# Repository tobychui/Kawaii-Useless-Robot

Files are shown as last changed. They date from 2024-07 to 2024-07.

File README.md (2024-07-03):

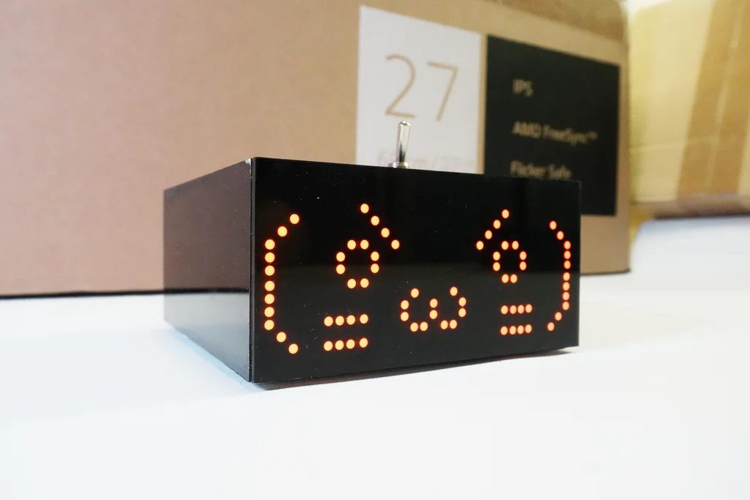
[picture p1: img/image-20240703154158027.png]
 

# Kawaii-Useless-Robot

A kawaii useless robot that runs away if you push it too hard

## Usage

There are three modes build into this robot. 

### Default Mode

Default mode is the mode where the robot interacts and response to switch pushing. To enter default mode, set the switch into the "OFF" position (lever pointing to the front-side of the robot) and power on the robot.

### AP Mode

AP mode is the mode where it will host a web server and you will be able to connect to it using mobile devices and control the robot movements and facial expression. 

For some devices like iPhone, you might need to disable mobile data and navigate to `http://192.168.4.1` with your browser to open the control panel. For most Android device, a captive portal notification should automatically pops up when you connects to it and ask you to sign in. The control UI will then be shown on the sign in captive portable browser if your network environment is valid.

### WiFi Debug Mode

You can enable WiFi (client) debug mode by setting `ENABLE_WIFI_DEBUG` to true with your home wifi crendentials.

```
#define ENABLE_WIFI_DEBUG false //Set to true to use WiFi Client mode for remote debugging
#define DEBUG_SSID "" //Debug SSID, usually your home WiFi SSID
#define DEBUG_PWD "" //Debug Password, your home WiFi Password
```

After this mode is enabled, you can connect to the web UI of the robot via your home local area network and debug any web interface issues.

## Prototype Video

IMAGE ALT TEXT HERE (https://youtu.be/l38ngzytmJw)

## Firmware Flashing

To flash firmware into this robot, open the top cover and use the type C port with a `</>` label for programming. The type C port at the back is for powering (and charging, if you builds has battery installed).

### Board Settings

ESP32 v2.014

- ESP32 Dev Module
- CPU Freq: 240Mhz
- Arduino & Events run on: Core 1
- Flash Mode: DIO

### Notes

Different version of ESP32 arduino core uses different version of RTOS. Thus, some version (specially the newer one) might have higher chances of crashing. After my testing, for the ESP32E I bought, the version v2.014 works the best. However, this might not be the same if you are getting an ESP32E with newer firmware.

## License

**Software**: MIT License

**Hardware**: CC BY-SA

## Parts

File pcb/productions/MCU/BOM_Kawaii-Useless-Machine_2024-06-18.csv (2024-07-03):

ID | Name | Designator | Footprint | Quantity | Manufacturer Part | Manufacturer | Supplier | Supplier Part | Price | link
1 | CONN-TH_2P-P2.50-XH2.54-2P | U9 | CONN-TH_2P-P2.50-XH2.54-2P | 1 | XH2.54*2P_直插 | null | LCSC | C9900008615 |  | https://lcsc.com/eda_search?q=C9900008615&%26type=1&ref=editor
2 | HDR-TH_2P-P2.54-V-M | P2 | HDR-TH_2P-P2.54-V-M | 1 | 2.54mm 1*2P | null | LCSC | C36717 | 0.006 | https://lcsc.com/eda_search?q=C36717&%26type=1&ref=editor
3 | R0805 | R34,R35,R32,R33 | R0805 | 4 | 0805W8F1002T5E | UNI-ROYAL(厚声) | LCSC | C17414 | 0.002 | https://item.szlcsc.com/142685.html
4 | C0805 | C28,C4,C7,C6,C8,C29 | C0805 | 6 | CL21A106KAYNNNE | SAMSUNG(三星) | LCSC | C15850 | 0.01 | https://item.szlcsc.com/373011.html
5 | SWITCH-SK12D07VG3 | SW1 | SWITCH-SK12D07VG3 | 1
6 | WIFI-SMD_ESP32-WROOM-32E-A | U4 | WIFI-SMD_ESP32-WROOM-32E-A | 1 | ESP32-WROOM-32E-N8R2 | ESPRESSIF(乐鑫) | LCSC | C5361945 | 3.587 | https://lcsc.com/eda_search?q=C2973652&%26type=1&ref=editor
7 | SOP-16_L10.0-W3.9-P1.27-LS6.0-BL | U7 | SOP-16_L10.0-W3.9-P1.27-LS6.0-BL | 1 |  |  | null |  |  | https://item.szlcsc.com/391677.html
8 | SOT-23-3_L2.9-W1.4-P1.90-LS2.6-BR | U11,U10 | SOT-23-3_L2.9-W1.4-P1.90-LS2.6-BR | 2 | BC817-16W | YANGJIE(扬杰) | LCSC | C968080 | 0.023 | https://atta.szlcsc.com/upload/public/pdf/source/20201201/C963380_48BF0C30091E539773A6B883B12108EF.pdf
9 | SOT-223-4_L6.5-W3.5-P2.30-LS7.0-BR | LDO1 | SOT-223-4_L6.5-W3.5-P2.30-LS7.0-BR | 1 | AMS1117-3.3 | AMS | LCSC | C6186 | 0.132 | https://item.szlcsc.com/84517.html
10 | IND-SMD_L7.3-W6.6 | L2 | IND-SMD_L7.3-W6.6 | 1 | MCS0630-1R0MPY1 | PSA(信昌电陶) | LCSC | C2937095 | 0.078 | https://lcsc.com/eda_search?q=C2937095&%26type=1&ref=editor
11 | R0805 | R5,R29 | R0805 | 2 | 0805W8F100KT5E | UNI-ROYAL(厚声) | LCSC | C25271 | 0.003 | https://lcsc.com/eda_search?q=C367831&%26type=1&ref=editor
12 | C0805 | C25,C26,C2,C23,C24 | C0805 | 5 | CC0805KRX7R9BB221 | YAGEO(国巨) | LCSC | C107145 | 0.006 | https://lcsc.com/eda_search?q=C123634&%26type=1&ref=editor
13 | C0805 | C27,C1 | C0805 | 2 | CL21A106KAYNNNE | SAMSUNG(三星) | LCSC | C15850 | 0.01 | https://lcsc.com/eda_search?q=C2835530&%26type=1&ref=editor
14 | LED0805-R-RD | LED1,LED2,LED3,LED4 | LED0805-R-RD | 4 | KT-0805W | KENTO | LCSC | C34499 | 0.016 | https://lcsc.com/eda_search?q=C84258&%26type=1&ref=editor
15 | ESOP-8_L4.9-W3.9-P1.27-LS6.0-BL-EP | U1 | ESOP-8_L4.9-W3.9-P1.27-LS6.0-BL-EP | 1 | IP5306 | INJOINIC(英集芯) | LCSC | C181692 | 0.258 | https://lcsc.com/eda_search?q=C181692&%26type=1&ref=editor
16 | R0805 | R3,R4,R1,R2 | R0805 | 4 | 0805W8F5101T5E | UNI-ROYAL(厚声) | LCSC | C27834 | 0.002 | https://lcsc.com/eda_search?q=C269736&%26type=1&ref=editor
17 | USB-C-SMD_TYPE-C-6PIN-2MD-073 | U3 | USB-C-SMD_TYPE-C-6PIN-2MD-073 | 1 | TYPE-C 16PIN 2MD(073) | SHOU HAN(首韩) | LCSC | C2765186 | 0.05 | https://lcsc.com/eda_search?q=C2765186&%26type=1&ref=editor
18 | C0805 | C3,C30 | C0805 | 2 | CC0805KRX7R9BB104 | YAGEO(国巨) | LCSC | C49678 | 0.004 | https://lcsc.com/eda_search?q=C2830721&%26type=1&ref=editor
19 | FPC-SMD_C20110 | P3,P4 | FPC-SMD_C20110 | 2 | 1.0-8P上接 | BOOMELE(博穆精密) | LCSC | C20110 | 0.09 | https://lcsc.com/eda_search?q=C20110&%26type=1&ref=editor
20 | R0805 | R6 | R0805 | 1 | RMCF0805ZT0R00 | SEI(Stackpole Electronics Inc.) | LCSC | C237773 | 0.005 | https://lcsc.com/eda_search?q=C237773&%26type=1&ref=editor
21 | TF-SMD_TF-012 | TF2 | TF-SMD_TF-012 | 1 |  |  |  |  |  | https://lcsc.com/eda_search?q=C5333937&%26type=1&ref=editor
22 | USB-C-TH_KH-TYPE-C-L6.9-6P | U6 | USB-C-TH_KH-TYPE-C-L6.9-6P | 1 | KH-TYPE-C-L6.9-6P | kinghelm(金航标) | LCSC | C2919657 | 0.137 | https://lcsc.com/eda_search?q=C2919657&%26type=1&ref=editor

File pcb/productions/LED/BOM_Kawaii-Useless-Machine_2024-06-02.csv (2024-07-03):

ID | Name | Designator | Footprint | Quantity | Manufacturer Part | Manufacturer | Supplier | Supplier Part | Price | JLCPCB Part Class | link
1 | MAX7219CWG+ | DM8,DM7,DM6,DM5,DM4,DM3,DM2,DM1 | SOIC-24_L15.4-W7.5-P1.27-LS10.3-BL | 8 | MAX7219CWG+T | ADI(亚德诺)/MAXIM(美信) | LCSC | C9964 | 2.425 | Extended Part | https://item.szlcsc.com/417060.html
2 | Header-Female-2.54_1x5 | CTRLIN | HDR-5X1/2.54 | 1 | 2.54mm 1*5p Female header | BOOMELE | LCSC | C50950 | 0.062
3 | 10uF | C1 | C0805 | 1 | CL21A106KAYNNNE | SAMSUNG(三星) | LCSC | C15850 | 0.011 | Extended Part | https://item.szlcsc.com/373011.html
4 | 100nF | C2 | C0805 | 1 | CC0805KRX7R9BB104 | YAGEO(国巨) | LCSC | C49678 | 0.004 | Extended Part | https://item.szlcsc.com/373011.html
5 | 788AS | U2,U3,U4,U5,U6,U7,U8,U1 | 788AS | 8
6 | 10kΩ | R1,R2,R3,R4,R5,R6,R7,R8 | R0805 | 8 | RMC080510K5%N | Tyohm(幸亚电阻) | LCSC | C269724 | 0.003 | Extended Part | https://lcsc.com/eda_search?q=C269724&%26type=1&ref=editor

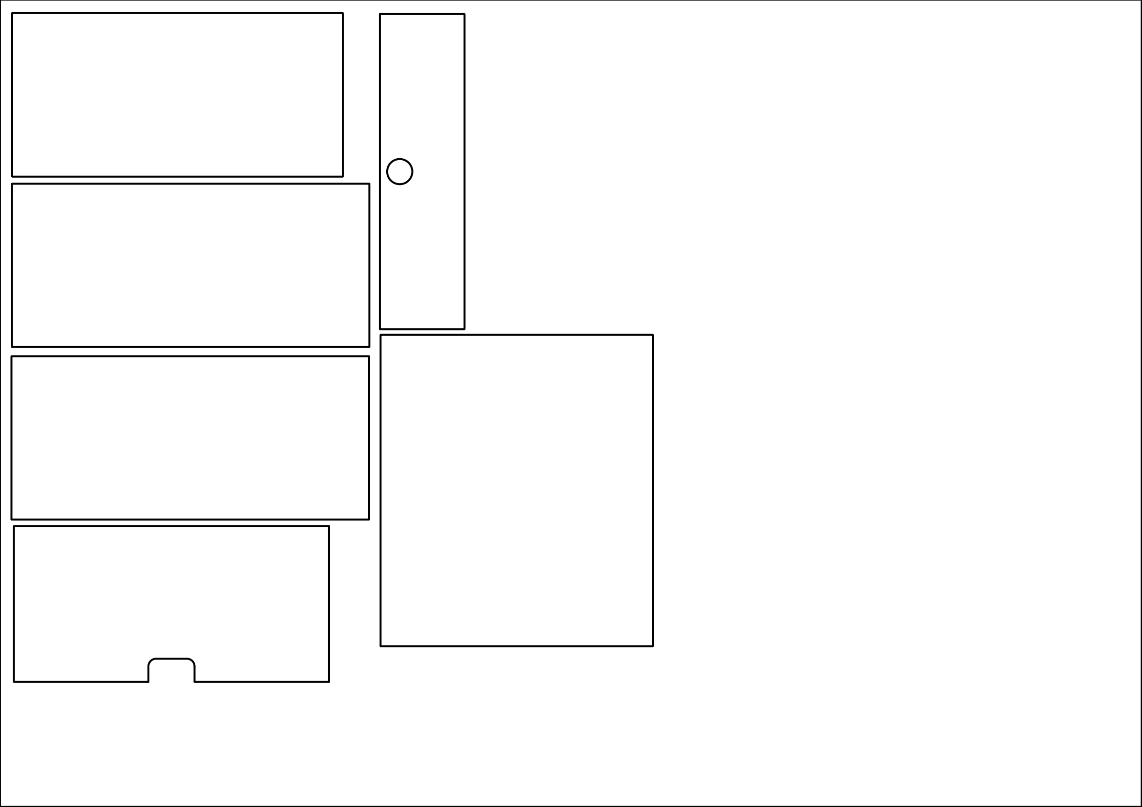
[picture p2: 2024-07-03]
lasercut/all-parts_v1-1.png

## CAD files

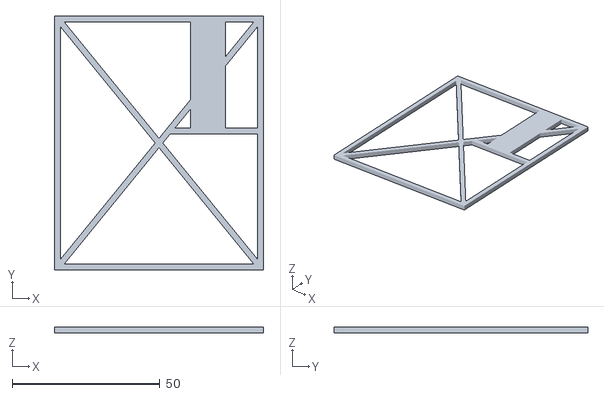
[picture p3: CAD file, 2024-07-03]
lasercut/validations/top-2.stl
70.8 x 86.0 x 2.00

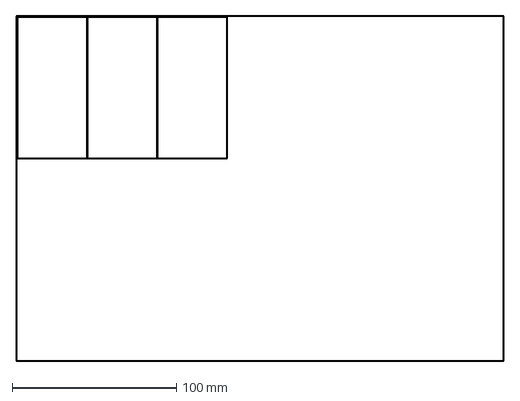
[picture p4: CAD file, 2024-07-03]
lasercut/黑透板.dxf
297.0 x 210.0 mm

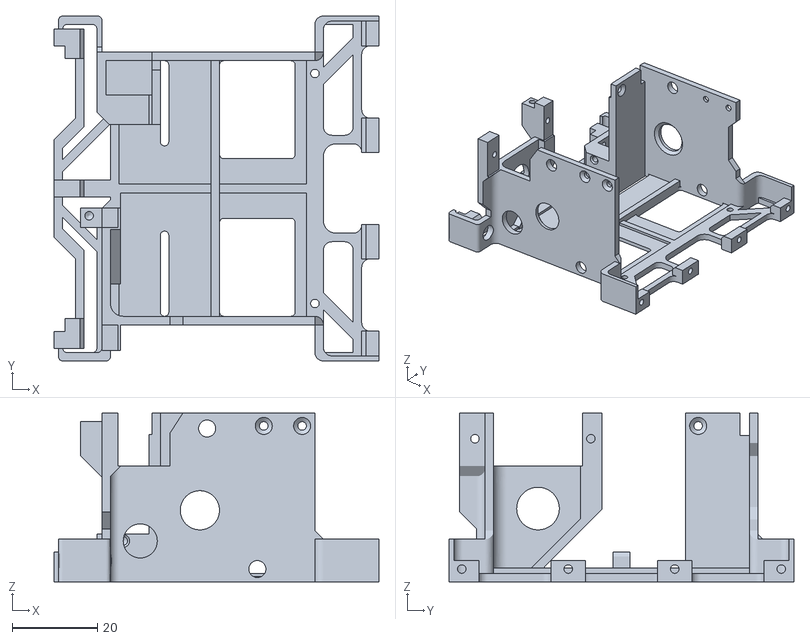
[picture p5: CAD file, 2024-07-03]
model/frame.stl
76.2 x 81.0 x 39.6

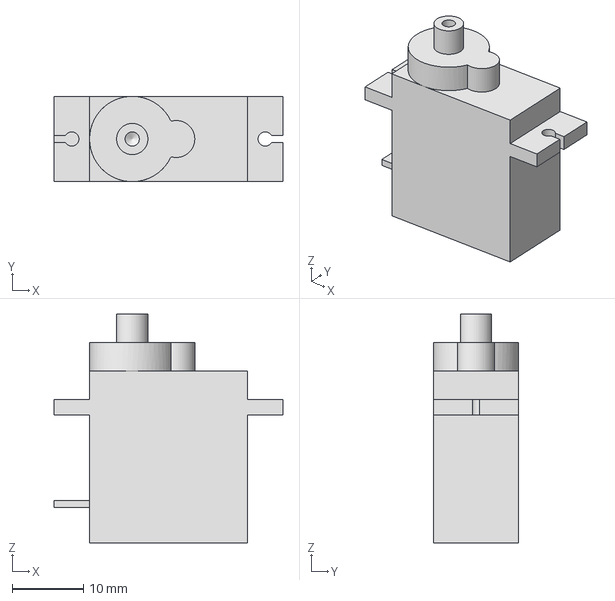
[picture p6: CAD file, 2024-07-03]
model/mockups/mg90s-servo.stp
32.2 x 12.0 x 32.2 mm

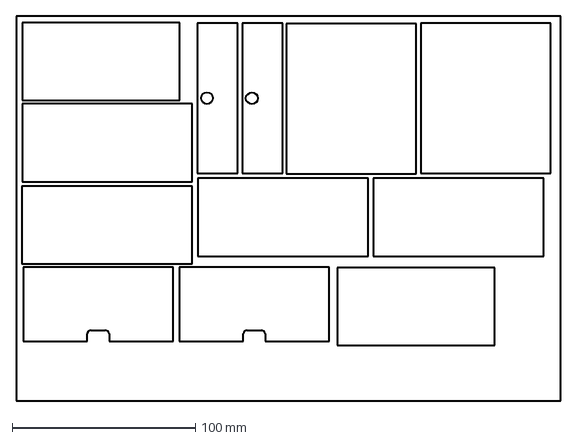
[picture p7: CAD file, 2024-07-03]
lasercut/all-parts_A4-fill.dxf
297.0 x 210.0 mm

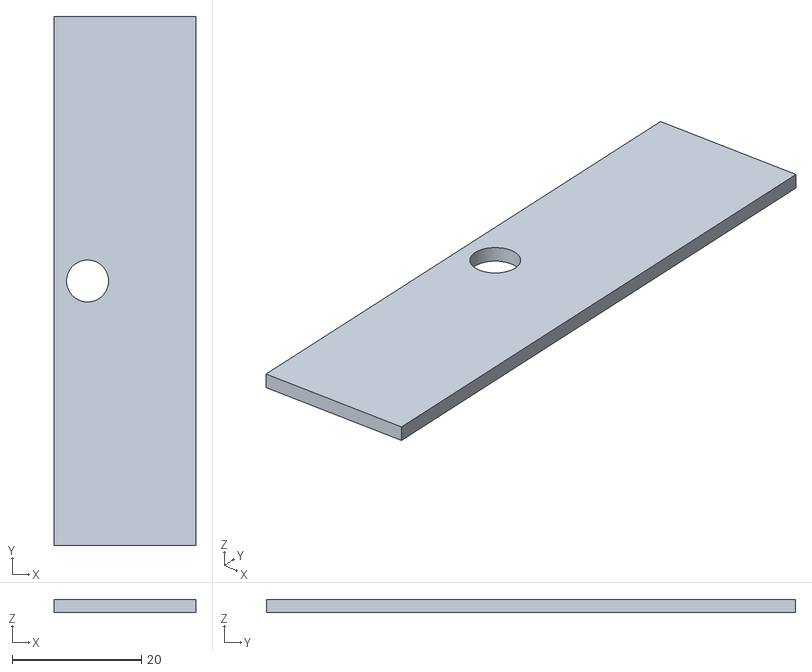
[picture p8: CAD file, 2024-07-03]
lasercut/validations/top-1.stl
22.0 x 82.0 x 2.00

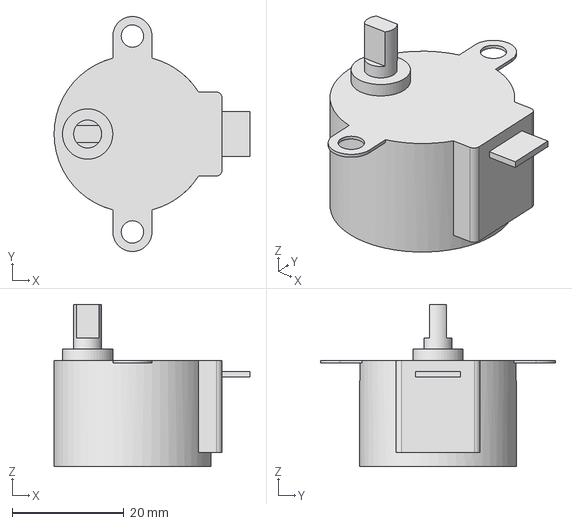
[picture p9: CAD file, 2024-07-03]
model/mockups/stepper-motor.stp
35.0 x 42.0 x 29.0 mm

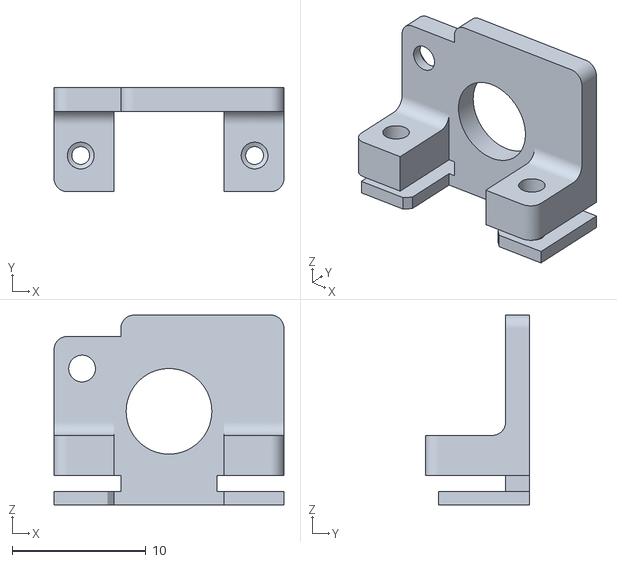
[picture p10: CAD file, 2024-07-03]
model/switch-mount.stl
17.2 x 7.80 x 14.2

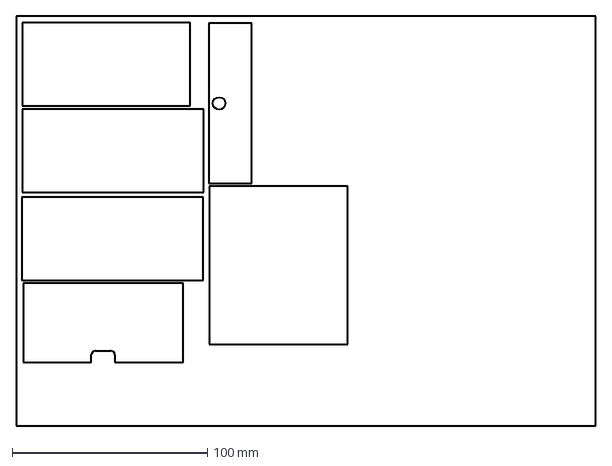
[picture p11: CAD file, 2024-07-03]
lasercut/all-parts_v1.dxf
297.0 x 210.0 mm

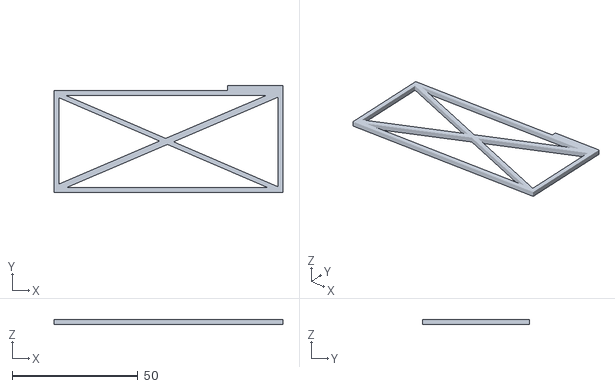
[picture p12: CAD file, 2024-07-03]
lasercut/validations/side-panels.stl
91.0 x 42.5 x 2.00

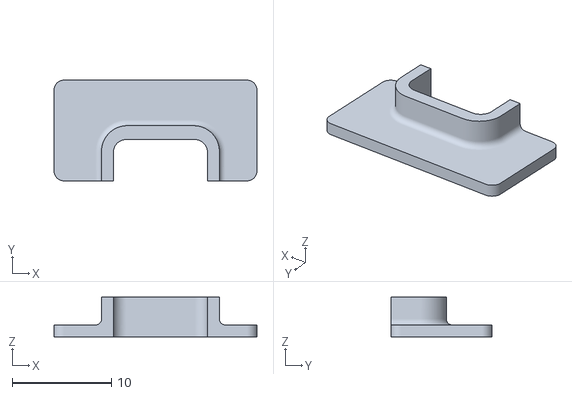
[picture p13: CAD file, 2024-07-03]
model/charge_support.stl
20.5 x 10.2 x 4.00

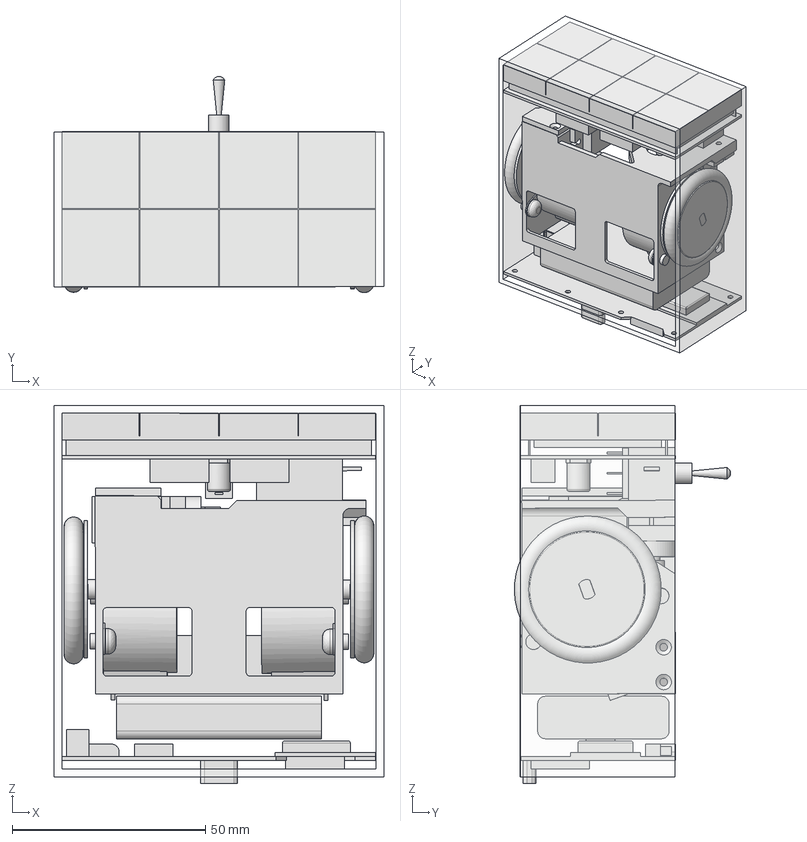
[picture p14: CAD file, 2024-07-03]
model/mockups/test-fit.stp
85.2 x 55.9 x 97.7 mm
display-unit
stepper-motor x 2
switch-mockup
mg90s-servo x 2
expected_size
battery_mockup
mcu-unit
frame v1
round m4x5 x 4
servo-mount
structural-bar
servo-swap x 2
wheel-mockup x 2
silicon-ring-mockup x 2

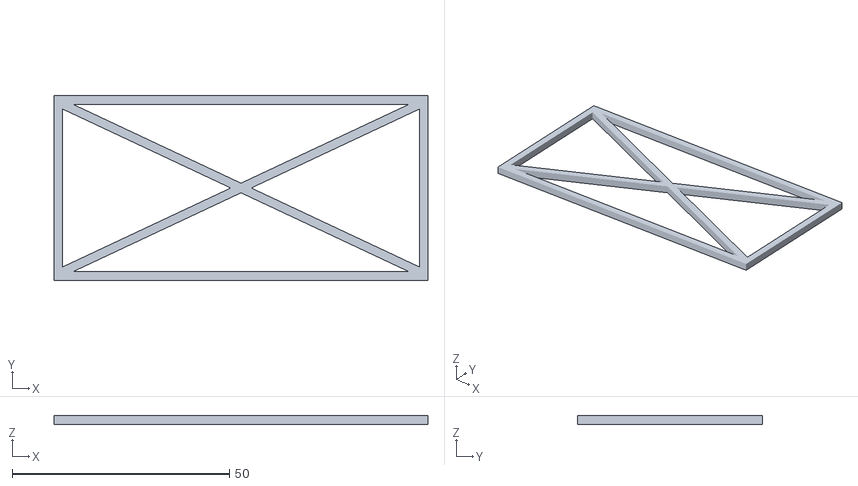
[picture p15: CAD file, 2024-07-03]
lasercut/validations/front-panel.stl
86.0 x 42.5 x 2.00

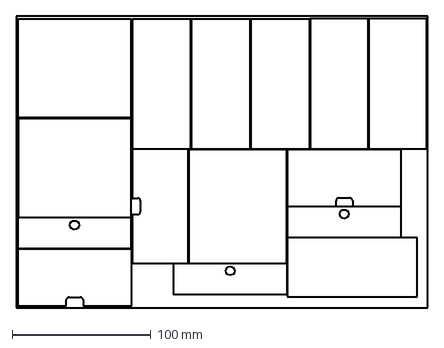
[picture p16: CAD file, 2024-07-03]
lasercut/黑板.dxf
297.0 x 210.0 mm

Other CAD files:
model/mockups/display-unit.stp
model/wheel.stl
lasercut/validations/back-panel.stl
model/mockups/switch-mockup.stp
lasercut/A4.ipt
lasercut/OldVersions/all-parts_A4-fill.0006.dwg
lasercut/OldVersions/all-parts_v1.0005.dwg
lasercut/OldVersions/all-parts_v2.0007.dwg
lasercut/OldVersions/back-panel.0008.ipt
lasercut/OldVersions/front-panel.0004.ipt
lasercut/OldVersions/side-panels.0013.ipt
lasercut/OldVersions/top-1.0008.ipt
lasercut/OldVersions/top-2.0004.ipt
lasercut/OldVersions/top-2.0006.ipt
lasercut/OldVersions/黑透板.0007.dwg
lasercut/all-parts_A4-fill.dwg
lasercut/all-parts_v1.dwg
lasercut/back-panel.ipt
lasercut/black-20x30.ipt
lasercut/front-panel.ipt
lasercut/side-panels.ipt
lasercut/top-1.ipt
lasercut/top-2.ipt
lasercut/黑板.dwg
lasercut/黑透板.dwg
model/charge_support.ipt
model/frame.ipt
model/frame_no-back-mount.ipt
model/mockups/M4x5flat.ipt
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

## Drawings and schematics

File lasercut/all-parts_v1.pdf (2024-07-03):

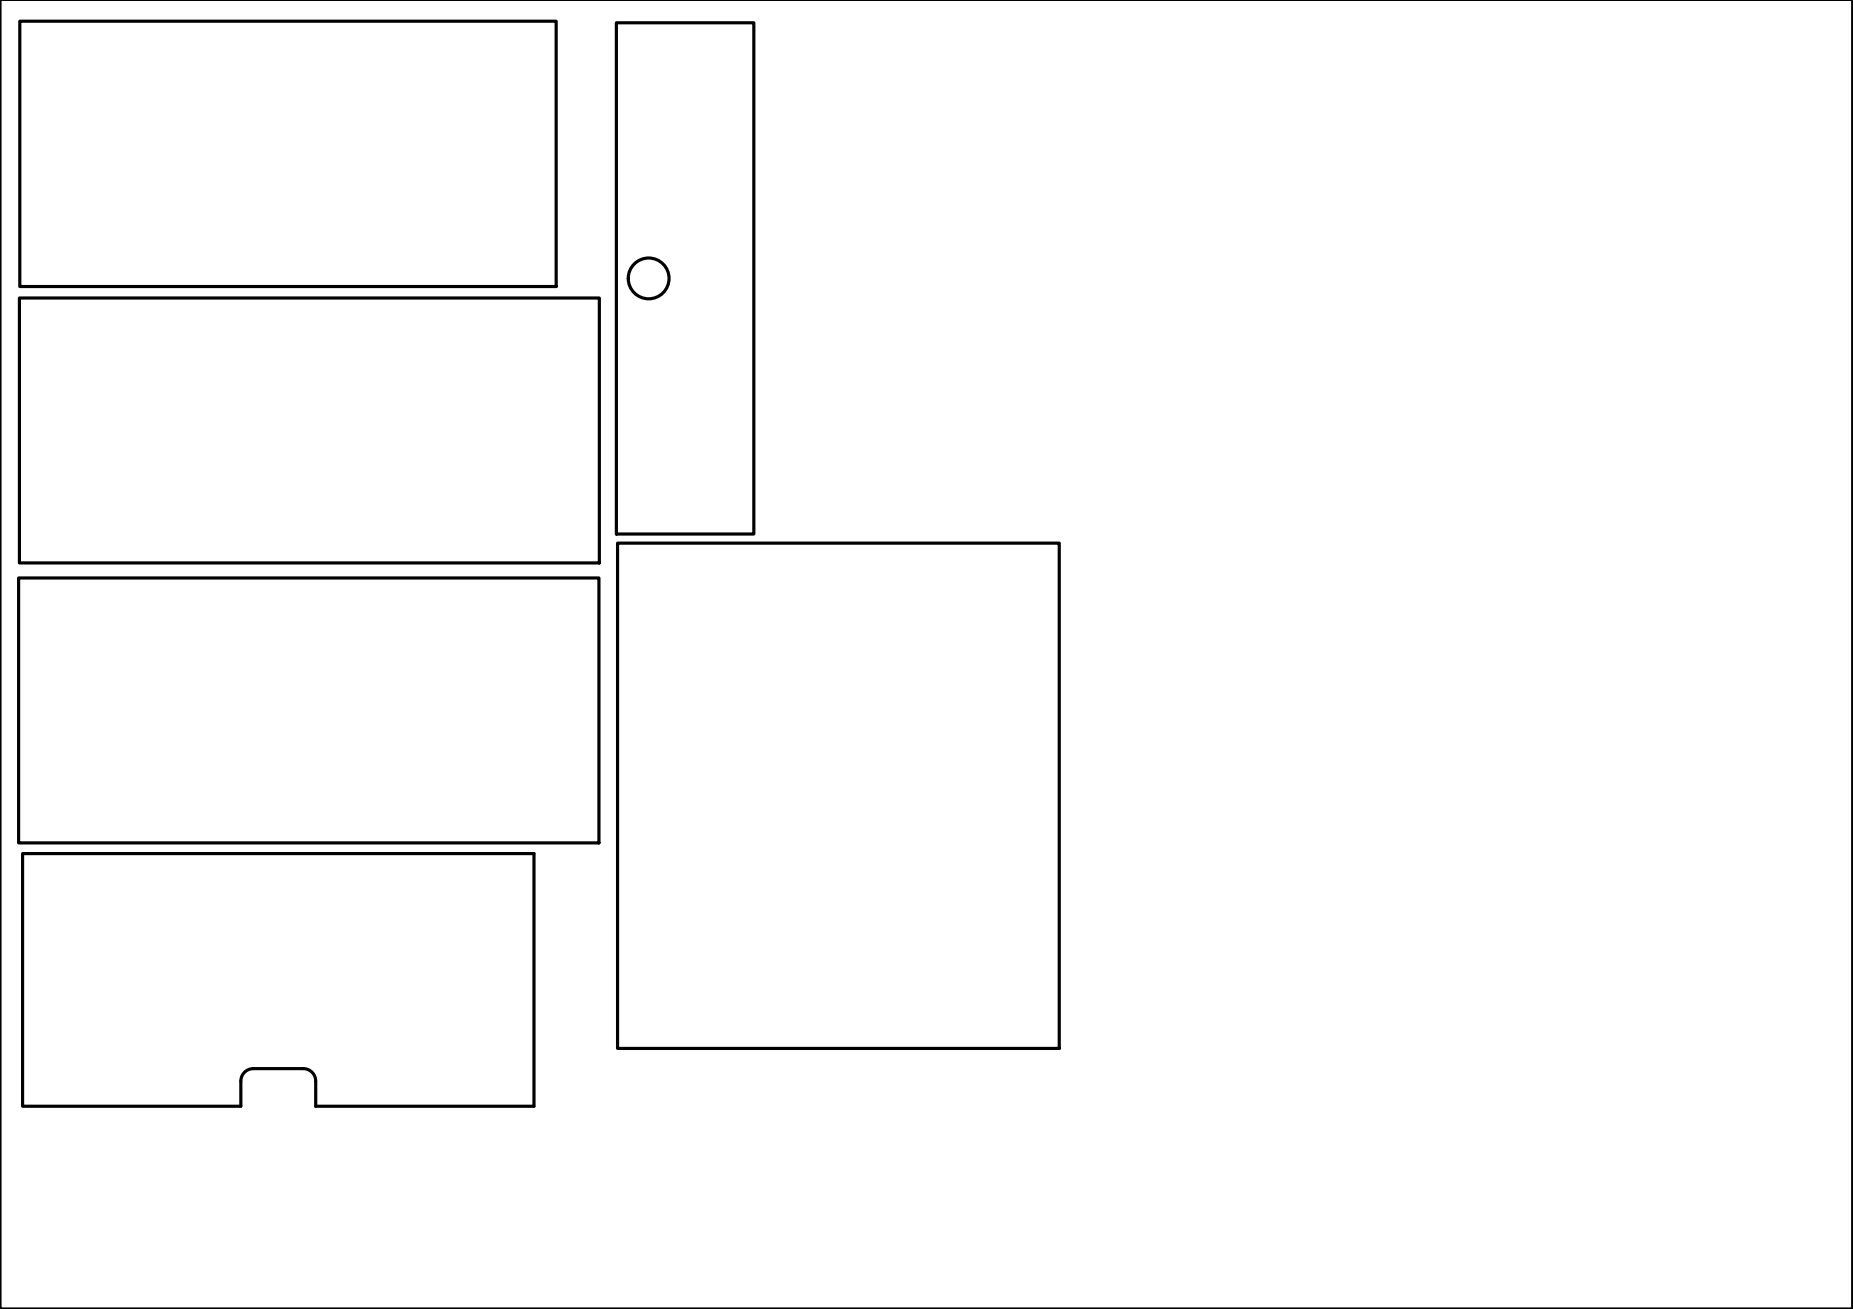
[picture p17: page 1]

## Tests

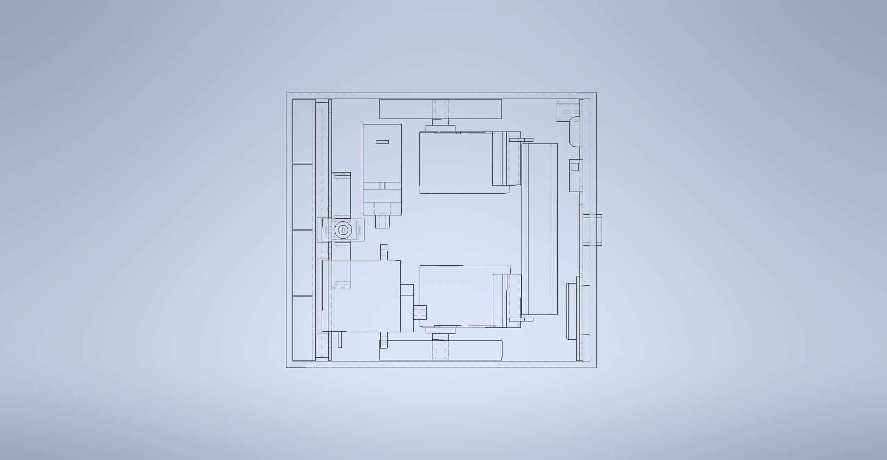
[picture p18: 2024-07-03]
model/mockups/test-fit.png

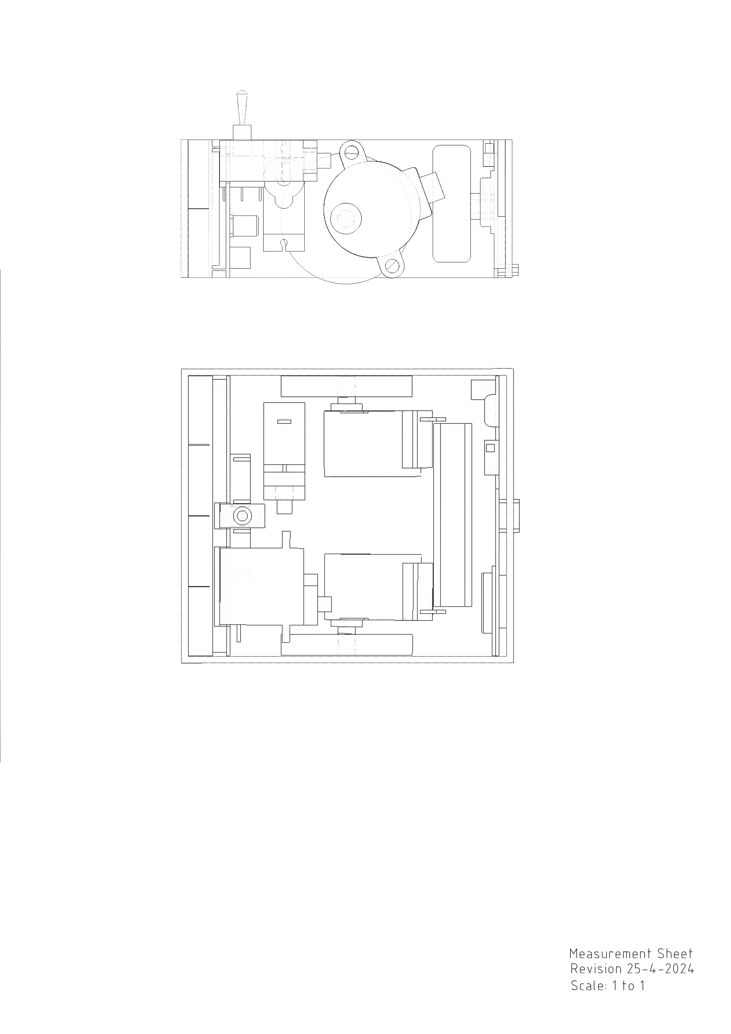
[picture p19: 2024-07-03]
model/drawings/testfit-25_4_2024.jpg

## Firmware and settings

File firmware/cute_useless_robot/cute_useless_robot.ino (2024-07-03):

/*

    Cute Useless Robot (´・ω・`)

    Developed by tobychui
    Idea come from Kairoshi

    Board Settings:
    ESP32 v2.014
    -> ESP32 Dev Module
    -> CPU Freq: 240Mhz
    -> Arduino & Events run on: Core 1
    -> Flash Mode: DIO
*/

/* Libraries */
#include <MD_MAX72xx.h>
#include <SPI.h>
#include <SD.h>
#include <FS.h>
#include <ESP32Servo.h>  //Require ESP32Servo
#include <WiFi.h>
#include <ESPAsyncWebServer.h>
#include <DNSServer.h>

/* Pins Definations */
#define STP_DATA_PIN 4    // Stepper Shift Register DS
#define STP_CLOCK_PIN 16  // Stepper Shift Register SH_CP
#define STP_LATCH_PIN 17  // Stepper Shift Register ST_CP

#define SERVO_SWITCH 27  //Servo to push the switch
#define SERVO_COVER 14   //Servo to push the cover

#define DP_CLK_PIN 32   //Display CLK
#define DP_DATA_PIN 33  //Display DIN
#define DP_CS_PIN 25    //Display CS

#define SD_CS_PIN 5       //SD Card CS pin
#define TOGGLE_SWITCH 13  //Switch on top of the matrix display

/* Display settings generated by trial and error. Don't touch these */
#define HARDWARE_TYPE MD_MAX72XX::DR1CR0RR0_HW
#define MAX_DEVICES 8

/* WiFI AP Settings */
#define AP_SSID "(´・ω・`)"
#define ENABLE_WIFI_DEBUG false //Set to true to use WiFi Client mode for remote debugging
#define DEBUG_SSID "" //Debug SSID, usually your home WiFi SSID
#define DEBUG_PWD "" //Debug Password, your home WiFi Password
AsyncWebServer server(80);
DNSServer dnsServer;

/* Calibrated offset for switch pusher servo, in degrees */
#define SERVO_ALIGNMENT_OFFSET 4

/* Hardware Type Definations */
Servo servoSwitchPusher;
Servo servoCoverPusher;
MD_MAX72XX mx = MD_MAX72XX(HARDWARE_TYPE, DP_DATA_PIN, DP_CLK_PIN, DP_CS_PIN, MAX_DEVICES);

/* Global Variables */
char animation = 'a';  //Animation ID to render
int movingDirection = 0; //Debug mode -> Moving direction
bool movingActive = false; //Debug mode -> Is Moving direction active

void setup() {
  delay(1000);
  Serial.begin(115200);

  // Allow allocation of all timers
  ESP32PWM::allocateTimer(0);
  ESP32PWM::allocateTimer(1);
  ESP32PWM::allocateTimer(2);
  ESP32PWM::allocateTimer(3);

  /* Stepper IO */
  pinMode(STP_DATA_PIN, OUTPUT);
  pinMode(STP_CLOCK_PIN, OUTPUT);
  pinMode(STP_LATCH_PIN, OUTPUT);
  standbySteppers();

  /* Servo IO */
  servoSwitchPusher.setPeriodHertz(50);
  servoCoverPusher.setPeriodHertz(50);
  servoSwitchPusher.attach(SERVO_SWITCH);
  servoCoverPusher.attach(SERVO_COVER);
  servoCoverPusher.write(0);
  servoSwitchPusher.write(0);

  /* Display Module */
  mx.begin();
  setDisplayBrightness(0x4);
  renderFrame();  //Render the default frame to matrix

  /* SD Card */
  // Initialize SD card
  if (!SD.begin(SD_CS_PIN, SPI, 4000000U, "/sd", 10U, false)) {
    Serial.println("[Error] Unable to mount SD card. Retrying in 10 seconds");
    loadSDErrorToFrameBuffer();  //Render SD ERROR to display
    renderFrame();

    //Retry in 10 seconds
    delay(5000);
    ESP.restart();
  }

  /* Start Dual-core processes */
  createSemaphore();
  startCoreTasks();
}

void loop() {
  //Process has been handled in tasks.ino
  //Do not use this loop
}

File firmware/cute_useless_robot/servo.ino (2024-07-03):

/*

  Servo Logic Code

  This script handles logic related to servo operations

*/

//Quickily push the switch back
void pushSwitchNow() {
  pushSwitchDelayed(270, 270);
}

//Push switch back with delay
void pushSwitchDelayed(int coverDelay, int pusherDelay) {
  servoCoverPusher.write(90);
  delay(coverDelay);
  servoSwitchPusher.write(130 + SERVO_ALIGNMENT_OFFSET);
  delay(pusherDelay);
  handlePushBackException(); //Check if switch is properly pushed back
  servoCoverPusher.write(0);
  servoSwitchPusher.write(0);
}

//Push with a pause before the switch is pushed
void pushWithHesitation() {
  servoCoverPusher.write(90);
  delay(1000);
  servoSwitchPusher.write(90 + SERVO_ALIGNMENT_OFFSET);
  delay(2000);
  servoSwitchPusher.write(130 + SERVO_ALIGNMENT_OFFSET);
  delay(1000);
  handlePushBackException(); //Check if switch is properly pushed back
  servoCoverPusher.write(0);
  servoSwitchPusher.write(0);
}

//Handle case where user hold the switch
void handlePushBackException() {
  bool switchPushed = getSwitchState();
  int triedResetCount = 0;
  if (switchPushed) {
    //Switch position still not reset. Wait and try again
    while (triedResetCount < 5) {
      switchPushed = getSwitchState();
      if (!switchPushed) {
        //Switch reset
        return;
      }
      if (triedResetCount < 1) {
        //Light push retry
        servoSwitchPusher.write(90 + SERVO_ALIGNMENT_OFFSET);
        delay(300);
        servoSwitchPusher.write(130 + SERVO_ALIGNMENT_OFFSET);
        delay(1000);
      }else if (triedResetCount < 3) {
        //Light push retry
        servoSwitchPusher.write(90 + SERVO_ALIGNMENT_OFFSET);
        delay(500);
        servoSwitchPusher.write(130 + SERVO_ALIGNMENT_OFFSET);
        delay(2000);
      } else {
        //Hard push retry
        servoSwitchPusher.write(0);
        delay(500);
        servoSwitchPusher.write(130 + SERVO_ALIGNMENT_OFFSET);
        delay(2000);
      }
      triedResetCount++;
    }

    //Max retry reached
    switchPushed = getSwitchState();
    if (switchPushed){
      char originalAnicode = animation;
      setAnimationCode('v');
      delay(5000);
      setAnimationCode(originalAnicode); //Restore the animation charcode
    }
   
    return;
  }
}

//Set the pusher servo to arm installation position
void setSwitchToInstallPosition() {
  servoSwitchPusher.write(125 + SERVO_ALIGNMENT_OFFSET);
}

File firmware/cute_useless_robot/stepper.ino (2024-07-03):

/* Stepper Drivers Functions */

//writeStep write the step given the byte representation of a step on both stepper
//e.g. writeStep(0b00110011);
void writeStep(byte stepByte) {
  shiftOut(STP_DATA_PIN, STP_CLOCK_PIN, MSBFIRST, stepByte);
  digitalWrite(STP_LATCH_PIN, HIGH);
  digitalWrite(STP_LATCH_PIN, LOW);
  delayMicroseconds(840); //780 - 800 ms minimum, recommend 840 to 860ms
}

//Set all coils to off and enter standby mode
//to save power and prevent overheating
void standbySteppers() {
  writeStep(0b00000000);
}

//Move the robot forward by 8 * rev micro steps
void forward(int rev) {
  for (int i = 0; i < rev; i++) {
    writeStep(0b00010001);
    writeStep(0b00110011);
    writeStep(0b00100010);
    writeStep(0b01100110);
    writeStep(0b01000100);
    writeStep(0b11001100);
    writeStep(0b10001000);
    writeStep(0b10011001);
  }
  standbySteppers();
}

//Move the robot backward by 8 * rev micro steps
void backward(int rev) {
  for (int i = 0; i < rev; i++) {
    writeStep(0b10011001);
    writeStep(0b10001000);
    writeStep(0b11001100);
    writeStep(0b01000100);
    writeStep(0b01100110);
    writeStep(0b00100010);
    writeStep(0b00110011);
    writeStep(0b00010001);
  }
  standbySteppers();
}

//Differential offset the robot wheels by +- 8 * rev micro steps, anti-clockwise
void rotateAntiClockwise(int rev) {
  for (int i = 0; i < rev; i++) {
    writeStep(0b00011001);
    writeStep(0b00111000);
    writeStep(0b00101100);
    writeStep(0b01100100);
    writeStep(0b01000110);
    writeStep(0b11000010);
    writeStep(0b10000011);
    writeStep(0b10010001);
  }
  standbySteppers();
}

//Differential offset the robot wheels by +- 8 * rev micro steps, clockwise
void rotateClockwise(int rev) {
  for (int i = 0; i < rev; i++) {
    writeStep(0b10010001);
    writeStep(0b10000011);
    writeStep(0b11000010);
    writeStep(0b01000110);
    writeStep(0b01100100);
    writeStep(0b00101100);
    writeStep(0b00111000);
    writeStep(0b00011001);
  }
  standbySteppers();
}
